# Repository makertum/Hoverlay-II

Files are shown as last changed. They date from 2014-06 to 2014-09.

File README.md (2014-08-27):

Hoverlay II
=================

<h3>Version 2.0</h3>
an modular, stackable open source vapor display.

<h2>License</h2>
All files licensed under GPL V3 http://www.gnu.org/licenses/gpl.html

<h2>BOM</h2>

<h3>Milled parts (for lasercuting: add drillholes), the material is 3mm PVC or acrylic (never put PVC into a lasercutter)</h3>
<ul>
	<li>1x becken-boden.dxf</li>
	<li>1x becken-seite-2x.dxf (contains two parts)</li>
	<li>1x becken-stirn-2x.dxf (contains two parts)</li>
	<li>1x kamin-2x.dxf (contains two parts)</li>
	<li>1x lufteinlass-2x.dxf (contains two parts)</li>
	<li>1x m-seite-logo-neu.dxf (logo is for engraving, not a cut-out)</li>
	<li>1x m-seite-schriftzug.dxf (text is for engraving, not a cut-out)</li>
	<li>2x m-stirn.dxf</li>
	<li>1x nebler-halter.dxf (contains 3 parts)</li>
</ul>

<h3>Printed parts</h3>
<ul>
	<li>12x stecker_halter.stl</li>
	<li>1x stromversorgung_1.stl</li>
	<li>1x stromversorgung_2.stl</li>
	<li>2x brightness_booster.stl (optional, for larger installations of 3+ Hoverlay II modules)</li>
	<li>4x supercomb_air.gcode (generated by supercomb_air.pde, a <a href="http://processing.org" target="_blank">processing</a> sketch)</li>
	<li>2x supercomb_fog.gcode (generated by supercomb_fog.pde, a <a href="http://processing.org" target="_blank">processing</a> sketch)</li>
</ul>

<h3>Other Materials</h3>
<ul>
	<li>4x ultrasonic atomizers</li>
	<li>1x 326mm long piece of ø25mm PVC tube (perforated with a driller) (optional/deprecated, use the brightness booster instead!)</li>
	<li>8x 80mm fans (min. 40 CFM)</li>
	<li>2x 60mm fans (for the brightness booster)</li>
	<li>2x male 3,5 mm rc car battery power connectors (for the brightness booster, i got <a href="http://www.pollin.de/shop/dt/Mzc4OTcxOTk-/Fundgrube/Modellbau/Goldkontakt_Steckerset_3_5_mm_5_Paare.html" target="_blank">these</a>)</li>
	<li>6x male 3,5 mm rc car battery power connectors (for the Hoverlay II module, i got <a href="http://www.pollin.de/shop/dt/Mzc4OTcxOTk-/Fundgrube/Modellbau/Goldkontakt_Steckerset_3_5_mm_5_Paare.html" target="_blank">these</a>)</li>
	<li>6x female 3,5 mm rc car battery power connectors (for the Hoverlay II module, i got <a href="http://www.pollin.de/shop/dt/Mzc4OTcxOTk-/Fundgrube/Modellbau/Goldkontakt_Steckerset_3_5_mm_5_Paare.html" target="_blank">these</a>)</li>
	<li>6x female 3,5 mm rc car battery power connectors (for the power supply connectors, i got <a href="http://www.pollin.de/shop/dt/Mzc4OTcxOTk-/Fundgrube/Modellbau/Goldkontakt_Steckerset_3_5_mm_5_Paare.html" target="_blank">these</a>)</li>
	<li>12x cable ring shoes (solder them to the connectors for attaching them to the stecker_halter.stl parts</li>
	<li>strong power cables, more cable shoes, solder</li>
	<li>plastics glue (for putting together the housing)</li>
	<li>double sided adhesive tape (for installing the supercombs)</li>
	<li>silicone (for water-tightening the vat, water tightening solder connections)</li>
	<li>various screws, length mostly dependend on your case-fan height</li>
	<li>appropriate power supplies for your electronics</li>
	<li>a video or still image projector. A 3000 ANSI lumen projector doesn't hurt while a overhead or dia projector will also work. LED projectors are not recommended, for holographic projections use a light-field projector and/or add a few drops of LSD to the vat*</li>
</ul>

<h2>Apps</h2>
Raw versions of all apps are now included in the repository. Mind that the code has not been cleaned up, so it might not run or export immediately, because of wrong serial port names, missing sound files, etc. Don't give up, it's easy to make them run, the code is quite straight forward.

<h2>To do</h2>
- [x] write a bom
- [x] nice power supply connector
- [ ] clean up apps code
- [ ] finish writing to do list

<h2>Credits and Licensing</h2>
Hoverlay II and all application code is licensed under <a href="http://www.gnu.org/licenses/gpl.html" target="_blank">GPL V3</a>. This project would not have
been possible without open source hard- and software. Special thanks the following open source projects, that have been used in making and/or are part of Hoverlay II:

<h3>Hardware Design:</h3>
<ul>
	<li><a href="http://www.openscad.org" target="_blank">OpenScad</a></li>
	<li><a href="http://www.processing.org" target="_blank">Processing</a></li>
</ul>
<h3>Manufacturing:</h3>
<ul>
	<li><a href="http://www.reprap.org" target="_blank">RepRap Project</a></li>
	<li><a href="http://www.repetier.com" target="_blank">Repetier</a></li>
	<li><a href="http://www.slic3r.org" target="_blank">Slic3r</a></li>
	<li><a href="http://linuxcnc.org" target="_blank">LinuxCNC</a></li>
</ul>

<h3>Application Development:</h3>
<ul>
	<li><a href="http://processing.org" target="_blank">Processing</a></li>
	<li><a href="http://kinecta.mihoo.de" target="_blank">KinectA</a> and <a href="https://github.com/OpenNI/OpenNI" target="_blank">OpenNI</a></li>
	<li><a href="https://github.com/memo/p5-MSAFluid" target="_blank">MSAFluid Processing library</a></li>
	<li><a href="http://www.sojamo.de/libraries/oscP5/" target="_blank">oscP5 Processing library</a></li>
	<li><a href="http://code.compartmental.net/tools/minim/" target="_blank">Minim Processing library</a></li>
	<li><a href="https://code.google.com/p/saitoobjloader/" target="_blank">saitoobjloader Processing library</a></li>
	<li><a href="http://arduino.cc/" target="_blank">Arduino</a></li>
</ul>

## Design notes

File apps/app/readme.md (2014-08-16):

put your exported app application files here. they will read the contents of the calibration, music and sounds subdirectories.

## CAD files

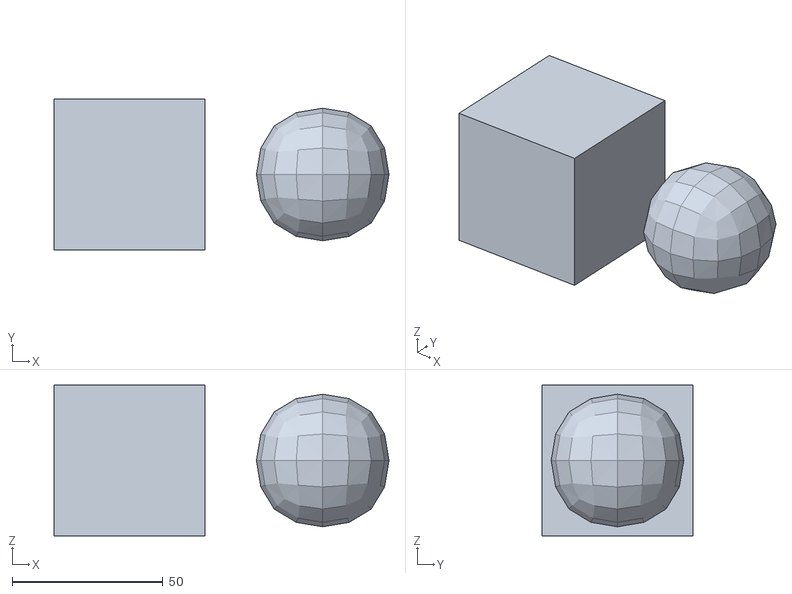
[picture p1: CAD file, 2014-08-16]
apps/sketch/Satellite/data/cube_sphere_test.obj
111.0 x 50.0 x 50.0

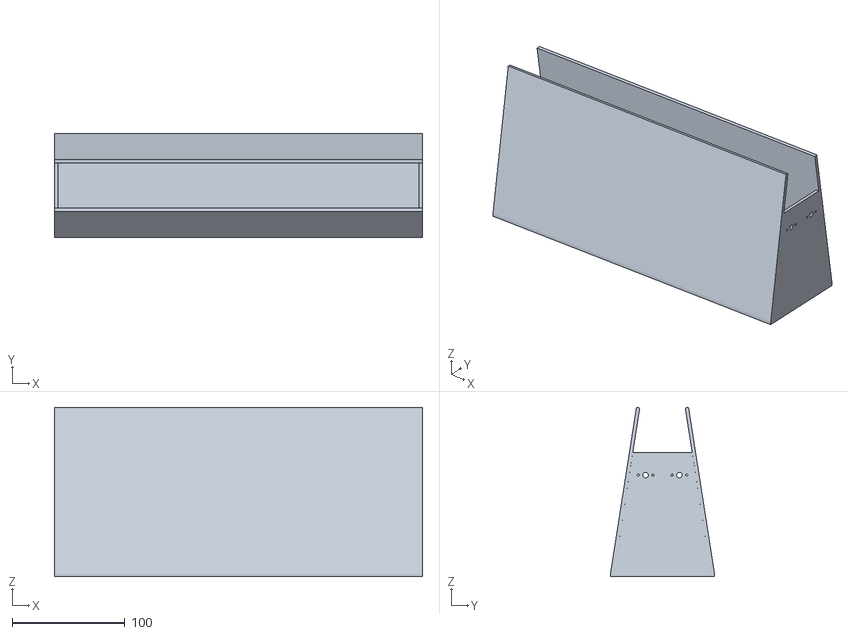
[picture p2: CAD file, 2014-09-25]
full_model/hoverlay_vat.stl
326.0 x 92.1 x 150.0

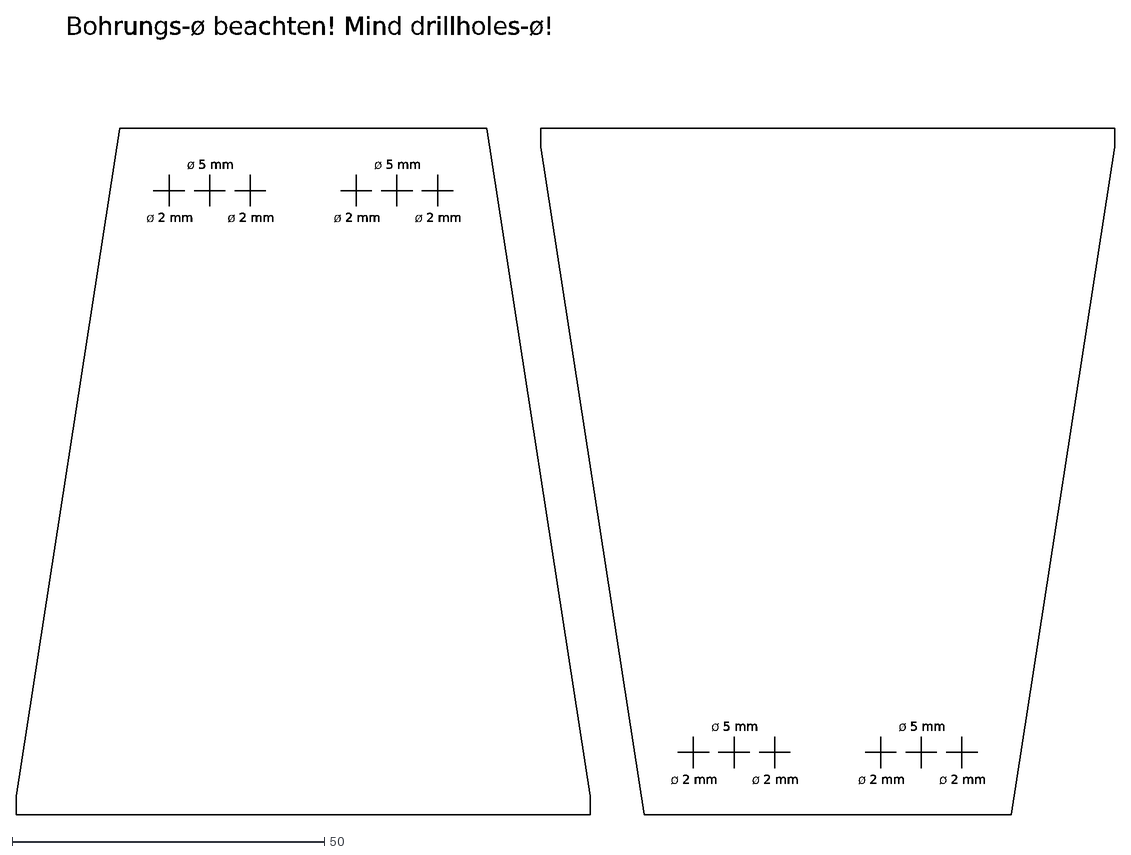
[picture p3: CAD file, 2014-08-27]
milling/dxf/becken-stirn-2x.dxf
ø 2 mm
ø 5 mm
Bohrungs-ø beachten! Mind drillholes-ø!

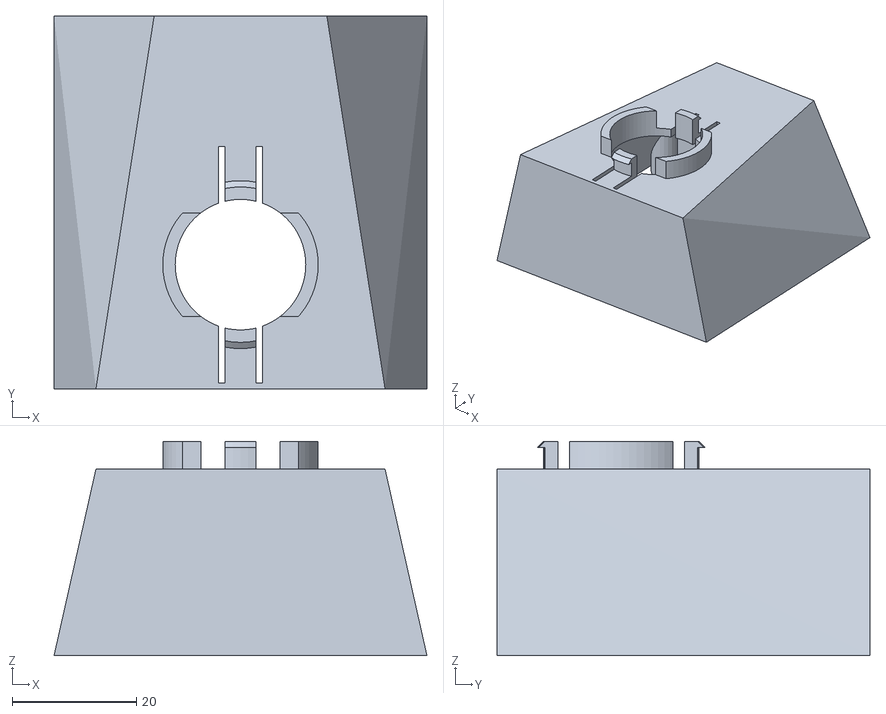
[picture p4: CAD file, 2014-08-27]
printing/brightness_booster/brightness_booster.stl
60.0 x 60.0 x 34.5

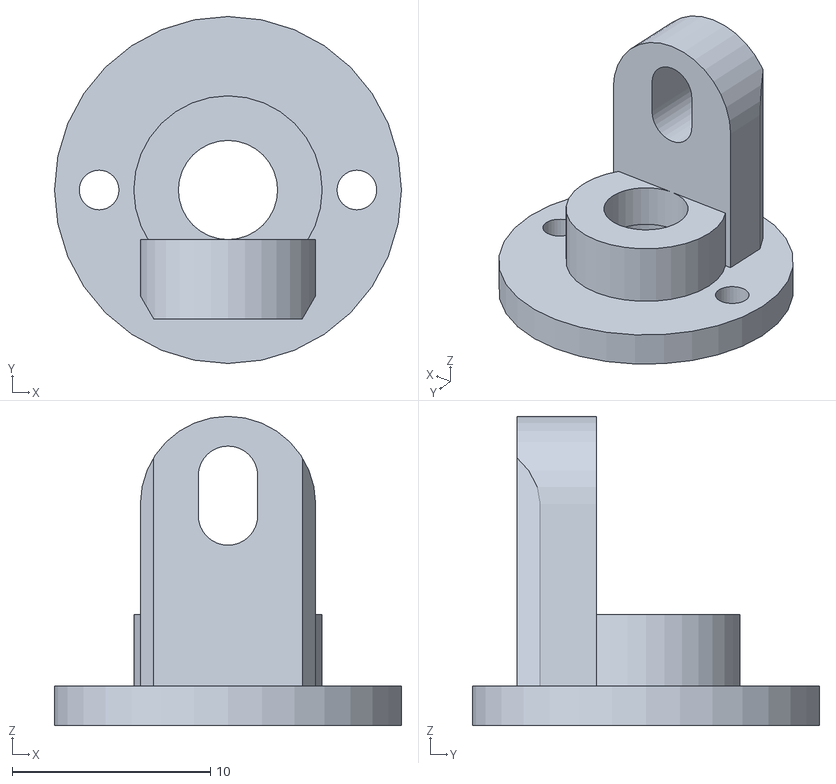
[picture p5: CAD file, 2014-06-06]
printing/stecker_halter/stecker_halter_2.stl
17.5 x 17.5 x 15.6

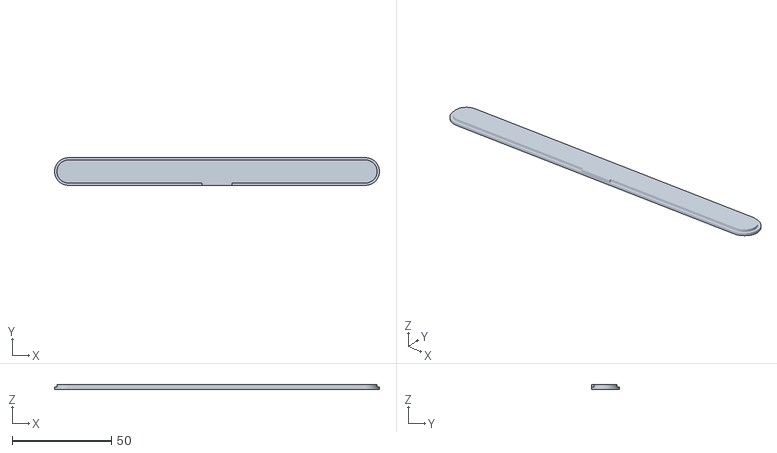
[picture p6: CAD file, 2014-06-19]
printing/stromversorgung/stromversorgung_top.stl
164.0 x 14.0 x 2.40

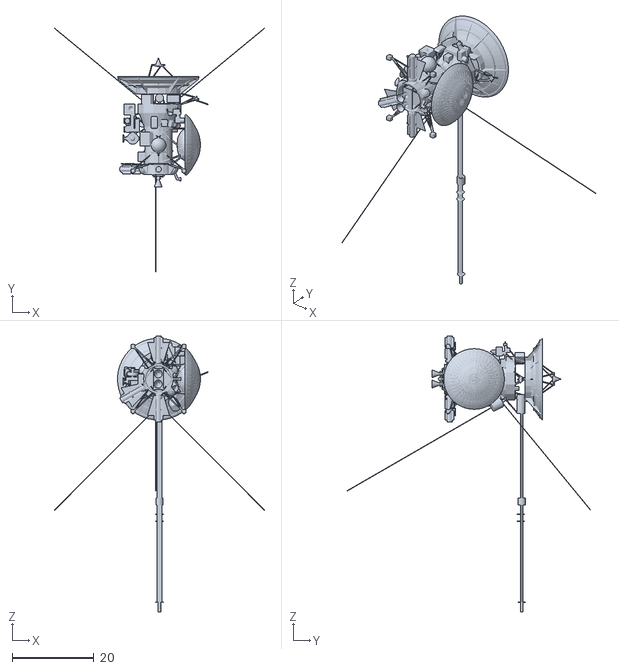
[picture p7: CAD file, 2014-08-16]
apps/sketch/Satellite/data/cassini.obj
51.4 x 59.6 x 67.5

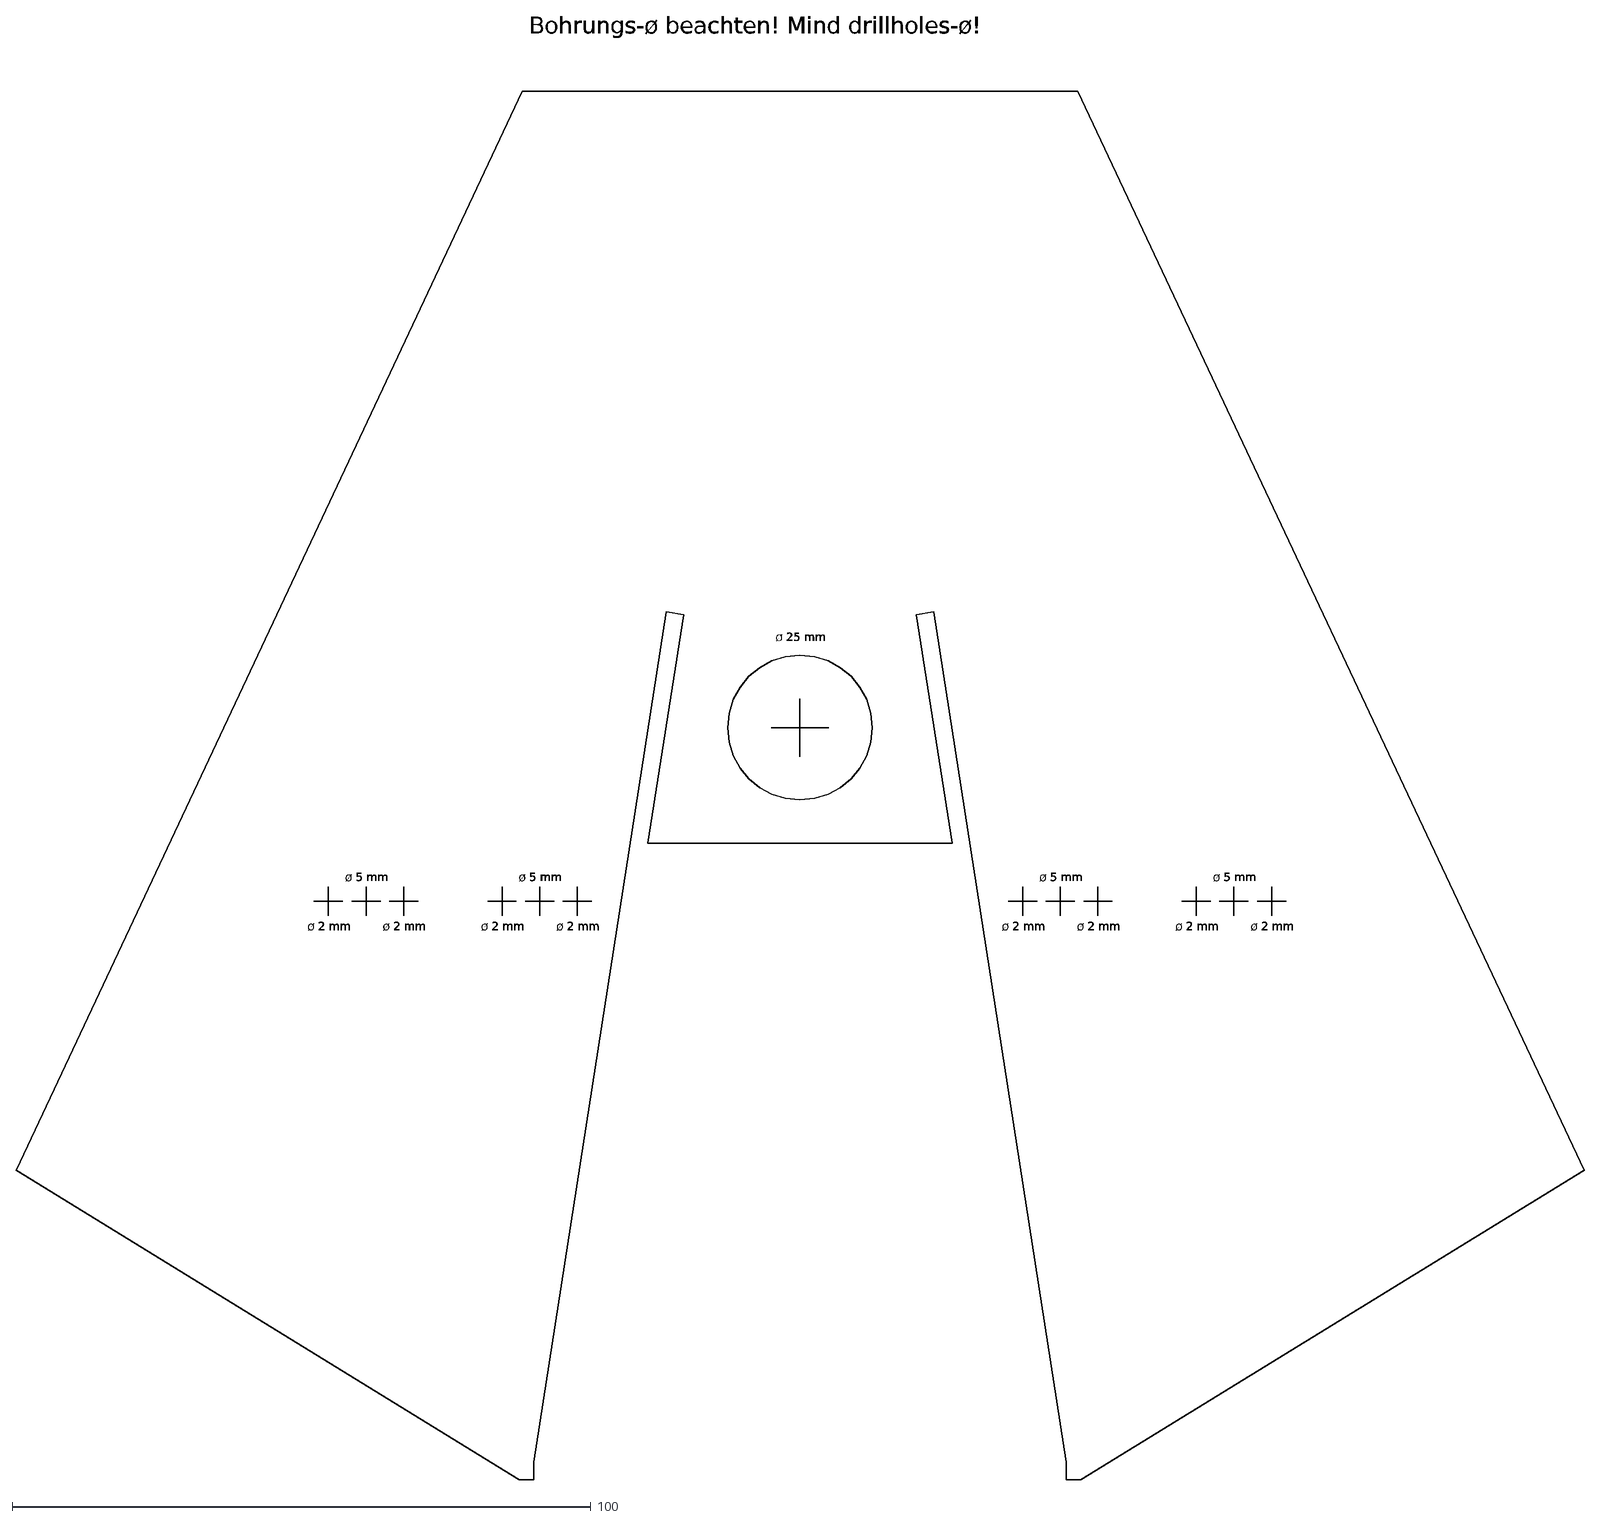
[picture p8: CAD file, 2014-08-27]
milling/dxf/m-stirn.dxf
Bohrungs-ø beachten! Mind drillholes-ø!
ø 2 mm
ø 5 mm
ø 25 mm

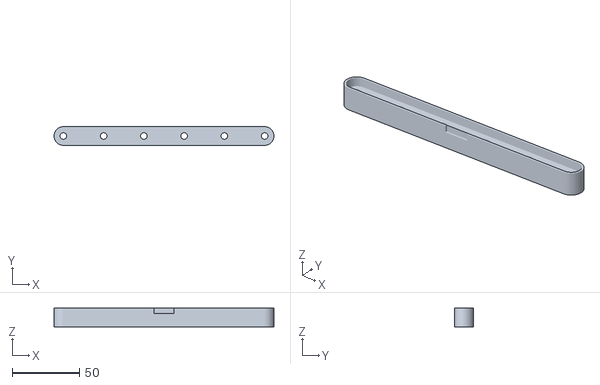
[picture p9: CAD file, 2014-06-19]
printing/stromversorgung/stromversorgung_case.stl
164.0 x 14.0 x 13.8

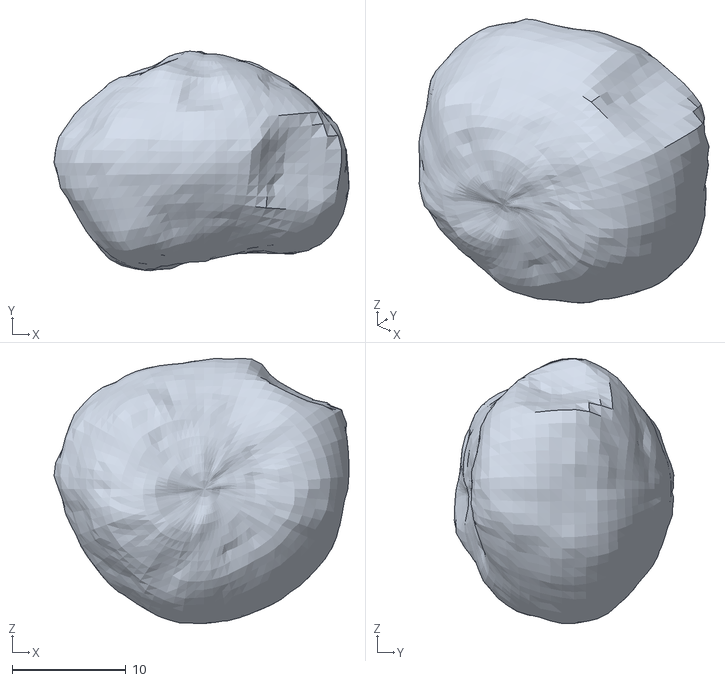
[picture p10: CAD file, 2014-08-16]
apps/sketch/Satellite/data/phobos.obj
26.0 x 19.3 x 23.4

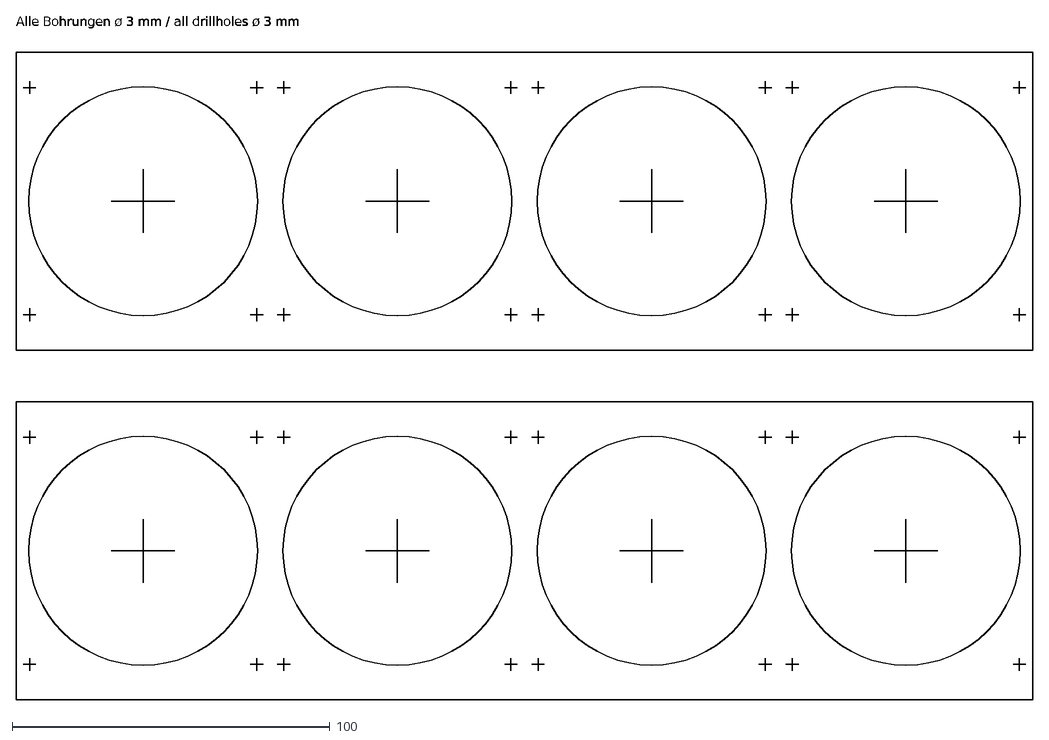
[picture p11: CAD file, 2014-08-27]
milling/dxf/lufteinlass-2x.dxf
Alle Bohrungen ø 3 mm / all drillholes ø 3 mm

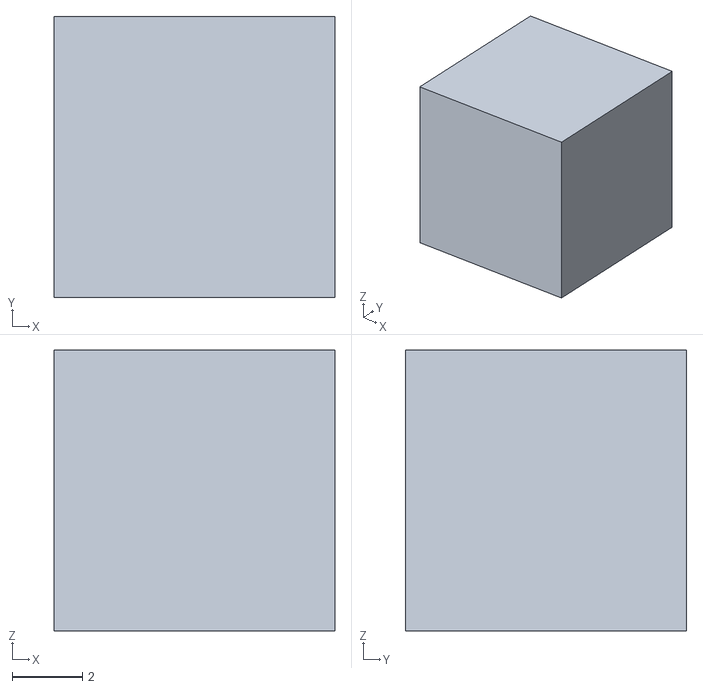
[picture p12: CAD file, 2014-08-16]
apps/sketch/Satellite/data/modo.obj
8.00 x 8.00 x 8.00

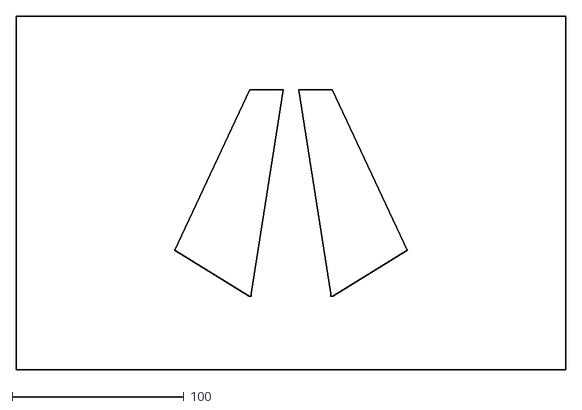
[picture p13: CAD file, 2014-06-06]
milling/dxf/m-seite-logo-neu.dxf
320.0 x 206.0

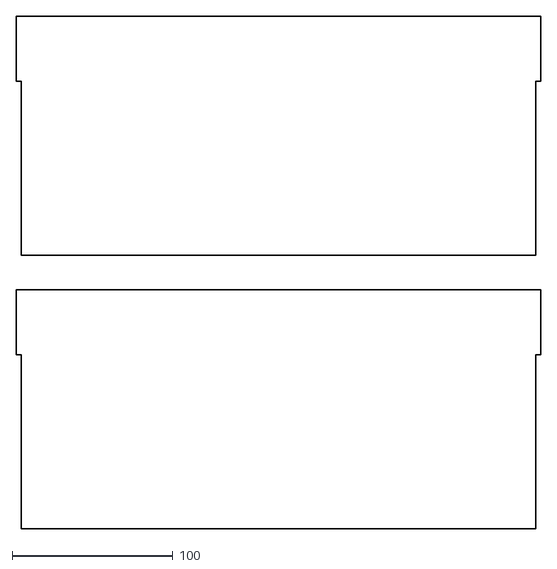
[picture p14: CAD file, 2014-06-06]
milling/dxf/becken-seite-2x.dxf
326.0 x 318.8

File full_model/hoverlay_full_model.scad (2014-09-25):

module side_plate(){
	difference(){
		translate([0,0,-3/2])
			linear_extrude(height=3){
				polygon(
					points=[
						[-48,140],		// 00
						[48,140],			// 01
						[135.5,-46.5],	// 02
						[48.5,-100],		// 03
						[46.036,-100],	// 04
						[46.036,-97],		// 05
						[23.087,50],		// 06
						[20.122,49.542],	// 07
						[26.295,10],		// 08
						[-26.295,10],		// 09
						[-20.122,49.542],// 10
						[-23.087,50],		// 11
						[-46.036,-97],	// 12
						[-46.036,-100],	// 13
						[-48.5,-100],		// 14
						[-135.5,-46.5],	// 15
						[-135.5,-46.5],	// 16
						[48,140],			// 17
					],
					paths=[
						[0,1,2,3,4,5,6,7,8,9,10,11,12,13,14,15,16,17]
					]
				);
			}
		translate([0,30,0])
			cylinder(r=25/2,h=3,center=true,$fn=32);
		translate([-75,-10,0]){
			cylinder(r=5/2,h=3,center=true,$fn=16);
				translate([-6.5,0,0])
					cylinder(r=2/2,h=3,center=true,$fn=16);
				translate([6.5,0,0])
					cylinder(r=2/2,h=3,center=true,$fn=16);
		}
		translate([-45,-10,0]){
			cylinder(r=5/2,h=3,center=true,$fn=16);
				translate([-6.5,0,0])
					cylinder(r=2/2,h=3,center=true,$fn=16);
				translate([6.5,0,0])
					cylinder(r=2/2,h=3,center=true,$fn=16);
		}
		translate([45,-10,0]){
			cylinder(r=5/2,h=3,center=true,$fn=16);
				translate([-6.5,0,0])
					cylinder(r=2/2,h=3,center=true,$fn=16);
				translate([6.5,0,0])
					cylinder(r=2/2,h=3,center=true,$fn=16);
		}
		translate([75,-10,0]){
			cylinder(r=5/2,h=3,center=true,$fn=16);
				translate([-6.5,0,0])
					cylinder(r=2/2,h=3,center=true,$fn=16);
				translate([6.5,0,0])
					cylinder(r=2/2,h=3,center=true,$fn=16);
		}
	}
}

module side_plates(){
	translate([-320/2-3/2,0,0])
		rotate([0,0,90])
			rotate([90,0,0])
				side_plate();
	translate([320/2+3/2,0,0])
		rotate([0,0,90])
			rotate([90,0,0])
				side_plate();
}


module logo_plates(){
	fpx1=65.639;
	fpy1=-95.582;
	fpx2=153.139;
	fpy2=90.918;
	angle=atan((fpy2-fpy1)/(fpx2-fpx1));
	fpoffy=-90.385;
	fpoffz=46.1;
	translate([0,fpoffy,fpoffz])
		rotate([angle,0,0])
			cube([320,206,3],center=true);
	translate([0,-fpoffy,fpoffz])
		rotate([-angle,0,0])
			cube([320,206,3],center=true);
}


module vent(){
	vx1=46.036;
	vy1=-97;
	vx2=23.087;
	vy2=50;
	angle=atan((vy2-vy1)/(vx2-vx1));
	voffy=14.626;
	voffz=75.024;
	translate([0,voffy,voffz])
		rotate([angle,0,0])
			cube([320,131.099,3],center=true);
	translate([0,-voffy,voffz])
		rotate([-angle,0,0])
			cube([320,131.099,3],center=true);
}

module air_inlets(){
	aix1=-132.38;
	aiy1=46.323;
	aix2=-42.322;
	aiy2=72.076;
	angle=atan((aiy2-aiy1)/(aix2-aix1));
	aioffy=88.4;
	aioffz=-59;
	translate([0,aioffy,aioffz])
		rotate([angle,0,0])
			air_inlet();
	translate([0,-aioffy,aioffz])
		rotate([-angle,0,0])
			air_inlet();
}

module air_inlet(){
	fan_size=80;
	fan_holes_dist=71.5;
	fan_inlet_diameter=70;
	difference(){
		cube([320,93.667,3],center=true);
		for(i=[-1.5:1.5]){
			translate([i*fan_size,0,0]){
				// FAN INLET
				cylinder(r=fan_inlet_diameter/2,h=3,center=true,$fn=32);
				// MOUNTING HOLES
				translate([-fan_holes_dist/2,-fan_holes_dist/2,0])
					cylinder(r=4/2,h=3,center=true,$fn=16);
				translate([fan_holes_dist/2,-fan_holes_dist/2,0])
					cylinder(r=4/2,h=3,center=true,$fn=16);
				translate([-fan_holes_dist/2,fan_holes_dist/2,0])
					cylinder(r=4/2,h=3,center=true,$fn=16);
				translate([fan_holes_dist/2,fan_holes_dist/2,0])
					cylinder(r=4/2,h=3,center=true,$fn=16);
			}
		}
	}
}

module housing(){
	union(){
		air_inlets();
		side_plates();
		logo_plates();
		vent();
		combs_fog();
		combs();
	}
}

module vat_side_plate(){
	difference(){
		translate([0,0,-3/2])
			linear_extrude(height=3){
				polygon(
					points=[
						[43,-97],		// 00
						[26.259,10],	// 01
						[-26.259,10],	// 02
						[-43,-97],	// 03
					],
					paths=[
						[0,1,2,3]
					]
				);
			}
		translate([-15,-10,0]){
			cylinder(r=5/2,h=3,center=true,$fn=16);
			translate([-6.5,0,0])
				cylinder(r=2/2,h=3,center=true,$fn=16);
			translate([6.5,0,0])
				cylinder(r=2/2,h=3,center=true,$fn=16);
	
		}
		translate([15,-10,0]){
			cylinder(r=5/2,h=3,center=true,$fn=16);
			translate([-6.5,0,0])
				cylinder(r=2/2,h=3,center=true,$fn=16);
			translate([6.5,0,0])
				cylinder(r=2/2,h=3,center=true,$fn=16);
		}
	}
}

module vat_side_plates(){
	translate([-320/2-3/2,0,0])
		rotate([0,0,90])
			rotate([90,0,0])
				vat_side_plate();
	translate([320/2+3/2,0,0])
		rotate([0,0,90])
			rotate([90,0,0])
				vat_side_plate();
}

module vat_hull(){
	rotate([0,90,0])
		rotate([0,0,90])
			translate([0,0,-326/2])
				linear_extrude(height=326){
					polygon(
						points=[
							[46.036,-100],	// 00
							[46.036,-97],		// 01
							[23.087,50],		// 02
							[20.122,49.542],	// 03
							[43,-97],			// 04
							[-43,-97],		// 05
							[-20.122,49.542],// 06
							[-23.087,50],		// 07
							[-46.036,-97],	// 08
							[-46.036,-100],	// 09
							[-48.5,-100],		// 10
						],
						paths=[
							[0,1,2,3,4,5,6,7,8,9,10]
						]
					);
				}
}

module vat(){
	union(){
		vat_side_plates();
		vat_hull();
	}
}

module combs(){
	vx1=46.036;
	vy1=-97;
	vx2=23.087;
	vy2=50;
	angle=90-atan((vy2-vy1)/(vx2-vx1));
	translate([-320/2,-12,100])
		rotate([angle,0,0])
			translate([0,0,-40])
				comb_air();
	translate([-320/2,12,100])
		rotate([-angle,0,0])
			translate([0,-39,-40])
				comb_air();
}

module comb_air(){
	include <elements/supercomb_air.scad>;
}

module combs_fog(){
	cfcells=60;
	cflength=320;
	cfheight=6;
	cfdepth=40;
	cfwalls=0.2;
	cfcellwidth=cflength/cfcells;
	union(){
		for(i=[-cfcells/2:cfcells/2-1]){
			translate([cfcellwidth/2+i*cfcellwidth,0,140-cfdepth/2])
				difference(){
					cube([cfcellwidth,cfheight,cfdepth],center=true);
					cube([cfcellwidth-2*cfwalls,cfheight-2*cfwalls,cfdepth],center=true);
				}
		}
	}
}
housing();
vat();

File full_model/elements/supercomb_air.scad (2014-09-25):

top_width=39;
bottom_width=39;
col_offset=0;
length=160;
height=40;
rows=12; // 16
cols=30; // 40
walls_bottom=0.3;
walls_top=0.3;
deflux=0.01;
//col_length=(length-walls)/cols;
col_length=4*(length)/(3*cols+0.5);
top_row_width=2*(top_width)/(rows+1);
bottom_row_width=2*(bottom_width)/(rows+1);

straws();
translate([length-0.125*col_length,0,0])
	straws();

module frame(){
	//real_length=col_length+(cols/2-1)*(col_length+0.5*col_length);
	real_length=length;
	box(points=[
		[
			0,
			col_offset,
			0
		],
		[
			real_length,
			col_offset,
			0
		],
		[
			real_length,
			bottom_width+col_offset,
			0
		],
		[
			0,
			bottom_width+col_offset,
			0
		],
		[
			0,
			0,
			height
		],
		[
			real_length,
			0,
			height
		],
		[
			real_length,
			top_width,
			height
		],
		[
			0,
			top_width,
			height
		]
	]);
}

module frame_cutout(){
	box(points=[
		[
			walls,
			col_offset+walls,
			0
		],
		[
			length-walls,
			col_offset+walls,
			0
		],
		[
			length-walls,
			bottom_width+col_offset-walls,
			0
		],
		[
			walls,
			bottom_width+col_offset-walls,
			0
		],
		[
			walls,
			walls,
			height
		],
		[
			length-walls,
			walls,
			height
		],
		[
			length-walls,
			top_width-walls,
			height
		],
		[
			walls,
			top_width-walls,
			height
		]
	]);
}

module straws(){
	union(){
		for(y=[0:2:rows-1]){
			for(x=[0:1:cols-1]){
				hexastraw(			
					x_bot=0.5*col_length+x*(3/4*col_length),
					y_bot=(x%2+y+1)*bottom_row_width/2+col_offset,
					z_bot=0,
					x_top=0.5*col_length+x*(3/4*col_length),
					y_top=(x%2+y+1)*top_row_width/2,
					z_top=height,
					w_bot=col_length+deflux,
					h_bot=bottom_row_width+deflux,
					w_top=col_length+deflux,
					h_top=top_row_width+deflux,
					walls_bot=walls_bottom,
					walls_top=walls_top
				);
			}
		}
	}
}

module box_ref(_length,_top_width,_bottom_width,_height,_offset){
	scaling_factor=_top_width/(_bottom_width+_offset);
	difference(){
		linear_extrude(height = _height, scale = [1,scaling_factor]){
			square ([_length,_bottom_width+_offset]);
		}
		translate([-_length,-_offset,-_height])
			linear_extrude(height = 3*_height, scale = [1,0])
				square ([3*_length,3*_offset]);
	}
}

module box(points=[[0,0,0],[100,0,0],[100,100,0],[0,100,0],[0,0,100],[100,0,100],[100,100,100],[0,100,100]]){
	polyhedron(
		points=[points[0],points[1],points[2],points[3],points[4],points[5],points[6],points[7]],
		triangles=[
			[0,5,1], // front
			[0,4,5], // front
			[3,6,7], // back
			[3,2,6], // back
			[7,5,4], // top
			[7,6,5], // top
			[1,3,0], // bottom
			[1,2,3], // bottom
			[7,0,3], // left
			[7,4,0], // left
			[5,2,1], // right
			[5,6,2]  // right
		]
	);
}

module hexagon(x_bot, y_bot, z_bot, x_top, y_top, z_top, w_bot, h_bot, w_top, h_top){
	//off_x_bot=sqrt(abs(pow(w_bot,2)-pow(h_bot,2)))/2;
	//off_x_top=sqrt(abs(pow(w_top,2)-pow(h_top,2)))/2;
	off_y_bot=h_bot/2;
	off_y_top=h_top/2;
	r_bot=w_bot/2;
	r_top=w_top/2;
	off_x_bot=0.5*r_bot;
	off_x_top=0.5*r_top;
	polyhedron(
		points=[
			// bottom
			[x_bot-r_bot,y_bot,z_bot],						// 0
			[x_bot-off_x_bot,y_bot+off_y_bot,z_bot],	// 1
			[x_bot+off_x_bot,y_bot+off_y_bot,z_bot],	// 2
			[x_bot+r_bot,y_bot,z_bot],						// 3
			[x_bot+off_x_bot,y_bot-off_y_bot,z_bot],	// 4
			[x_bot-off_x_bot,y_bot-off_y_bot,z_bot],	// 5
			// top
			[x_top-r_top,y_top,z_top],						// 6
			[x_top-off_x_top,y_top+off_y_top,z_top],	// 7
			[x_top+off_x_top,y_top+off_y_top,z_top],	// 8
			[x_top+r_top,y_top,z_top],						// 9
			[x_top+off_x_top,y_top-off_y_top,z_top],	// 10
			[x_top-off_x_top,y_top-off_y_top,z_top]		// 11
		],
		faces=[
			[0,7,6],
			[0,1,7],
			[1,8,7],
			[1,2,8],
			[2,9,8],
			[2,3,9],
			[10,9,3],
			[10,3,4],
			[11,4,5],
			[11,10,4],
			[6,5,0],
			[6,11,5],
			[11,6,7],
			[11,7,8],
			[11,8,10],
			[10,8,9],
			[5,1,0],
			[5,2,1],
			[5,4,2],
			[4,3,2]
		]
	);
}

module hexastraw(x_bot, y_bot, z_bot, x_top, y_top, z_top, w_bot, h_bot, w_top, h_top,walls_bot,walls_top){
	angle_bot=atan(h_bot/w_bot);
	angle_top=atan(h_top/w_top);
	walls_corr_bot=(h_bot-walls_bot)/h_bot;
	walls_corr_top=(h_top-walls_top)/h_top;

	difference(){
		hexagon(
			x_bot=x_bot,
			y_bot=y_bot,
			z_bot=z_bot,
			x_top=x_top,
			y_top=y_top,
			z_top=z_top,
			w_bot=w_bot,
			h_bot=h_bot,
			w_top=w_top,
			h_top=h_top
		);
		hexagon(
			x_bot=x_bot,
			y_bot=y_bot,
			z_bot=z_bot,
			x_top=x_top,
			y_top=y_top,
			z_top=z_top,
			w_bot=w_bot*walls_corr_bot,
			h_bot=h_bot-walls_bot,
			w_top=w_top*walls_corr_top,
			h_top=h_top-walls_top
		);
	}
}

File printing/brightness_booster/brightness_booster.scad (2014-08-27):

// Hoverlay II brighntness booster mk1
// created by Moritz Walter, 2014
// licensed under GPL V3
// all infos at iamnotachoice.com/hoverlay-2

// BASIC CONFIGURATION

fan_size=60; // select your fan size (in mm) here from 40, 60 or 80 (other values won't work!)

walls=1;	// thickness of printed walls
base=2;	// thickness of printed baseplate (must be a bit thicker because we're printing bridges here)
fan_dist=30;	// distance between fan and hoverlay side panel
fan_screw_diameter=2.5; // how large are your screws
fan_screw_length=8;	// how long are your screws (should be 8mm screws)
fan_screw_nipple_diameter=6; // how strong are the screw nipples ;)
fan_screw_nipple_length=fan_dist;
tube_walls=2;
tube_length=3.5;

// EXTENDED CONFIGURATION

hole_diameter=25;
snappy_diameter=27;
snappy_width=5;
snappy_clearance=1;
snappy_bendable=38;

// CONSTANTS

fan_screw_dist_80mm=71.5;
fan_screw_dist_60mm=50;
fan_screw_dist_40mm=32;

housing_p0_40mm=[-17.014,20,0];
housing_p1_40mm=[17.014,20,0];
housing_p0_60mm=[-13.892,40,0];
housing_p1_60mm=[13.892,40,0];
housing_p0_80mm=[-10.77,60,0];
housing_p1_80mm=[10.77,60,0];
housing_p2=[23.259,-20,0];
housing_p3=[-23.259,-20,0];

// PREPROCESSING

housing_p0i_40mm=[housing_p0_40mm[0]+walls,housing_p0_40mm[1]-walls,base];
housing_p1i_40mm=[housing_p1_40mm[0]-walls,housing_p1_40mm[1]-walls,base];

housing_p0i_60mm=[housing_p0_60mm[0]+walls,housing_p0_60mm[1]-walls,base];
housing_p1i_60mm=[housing_p1_60mm[0]-walls,housing_p1_60mm[1]-walls,base];

housing_p0i_80mm=[housing_p0_80mm[0]+walls,housing_p0_80mm[1]-walls,base];
housing_p1i_80mm=[housing_p1_80mm[0]-walls,housing_p1_80mm[1]-walls,base];

housing_p2i=[housing_p2[0]-walls,housing_p2[1]+walls,base];
housing_p3i=[housing_p3[0]+walls,housing_p3[1]+walls,base];

fan_center=[(housing_p2[0]+housing_p3[0])/2,(housing_p2[1]+housing_p3[1])/2+fan_size/2,fan_dist];

fan_p0=[fan_center[0]-fan_size/2,fan_center[1]+fan_size/2,fan_center[2]];
fan_p1=[fan_center[0]+fan_size/2,fan_center[1]+fan_size/2,fan_center[2]];
fan_p2=[fan_center[0]+fan_size/2,fan_center[1]-fan_size/2,fan_center[2]];
fan_p3=[fan_center[0]-fan_size/2,fan_center[1]-fan_size/2,fan_center[2]];

fan_p0i=[fan_center[0]-fan_size/2+walls,fan_center[1]+fan_size/2-walls,fan_center[2]];
fan_p1i=[fan_center[0]+fan_size/2-walls,fan_center[1]+fan_size/2-walls,fan_center[2]];
fan_p2i=[fan_center[0]+fan_size/2-walls,fan_center[1]-fan_size/2+walls,fan_center[2]];
fan_p3i=[fan_center[0]-fan_size/2+walls,fan_center[1]-fan_size/2+walls,fan_center[2]];

// TEH CODE

module tube_cutout(){
	translate([0,0,base/2])
		cylinder(r=hole_diameter/2-tube_walls,h=base,center=true, $fn=64);
}

module tube(){
	translate([0,0,-tube_length/2-walls/2])
			intersection(){
				difference(){
					cylinder(r=hole_diameter/2,h=tube_length+walls,center=true, $fn=64);
					cylinder(r=hole_diameter/2-tube_walls,h=tube_length+walls,center=true, $fn=64);
				}
			cube([hole_diameter,2/3*hole_diameter,tube_length+walls],center=true);
		}
}

module snappy(){
		intersection(){
			union(){
				translate([0,0,-tube_length-walls/2])
					difference(){
						cylinder(r1=hole_diameter/2,r2=snappy_diameter/2,h=walls,center=true, $fn=64);
						cylinder(r=hole_diameter/2-tube_walls,h=walls,center=true, $fn=64);
					}
				translate([0,0,-tube_length/2-walls/2])
					difference(){
						cylinder(r=hole_diameter/2,h=tube_length+walls,center=true, $fn=64);
						cylinder(r=hole_diameter/2-tube_walls,h=tube_length+walls,center=true, $fn=64);
					}
			}
			translate([0,0,-tube_length/2-walls/2])
			cube([snappy_width,snappy_diameter,tube_length+walls],center=true);
		}
}

module snappy_cutout(){
	translate([snappy_width/2+snappy_clearance/2,0,base/2])
		cube([snappy_clearance,snappy_bendable,base],center=true);
	translate([-snappy_width/2-snappy_clearance/2,0,base/2])
		cube([snappy_clearance,snappy_bendable,base],center=true);
	
}


module duct(){
	difference(){
		union(){
			difference(){
				if (fan_size==40){
					difference(){
						outer_duct(housing_p0_40mm, housing_p1_40mm);
						inner_duct(housing_p0i_40mm, housing_p1i_40mm);
					}
				} else if (fan_size==60){
					difference(){
						outer_duct(housing_p0_60mm, housing_p1_60mm);
						inner_duct(housing_p0i_60mm, housing_p1i_60mm);
					}
				} else if (fan_size==80){
					difference(){
						outer_duct(housing_p0_80mm, housing_p1_80mm);
						inner_duct(housing_p0i_80mm, housing_p1i_80mm);
					}
				}
				tube_cutout();
				snappy_cutout();
			}
			if (fan_size==40){
				screw_nipples(fan_screw_dist_40mm);
			} else if (fan_size==60){
				screw_nipples(fan_screw_dist_60mm);
			} else if (fan_size==80){
				screw_nipples(fan_screw_dist_80mm);
			}
		}
		if (fan_size==40){
			screw_cutouts(fan_screw_dist_40mm);
		} else if (fan_size==60){
			screw_cutouts(fan_screw_dist_60mm);
		} else if (fan_size==80){
			screw_cutouts(fan_screw_dist_80mm);
		}
	}
}

module inner_duct(housing_p0i, housing_p1i){
	polyhedron(
		points=[
			housing_p0i,
			housing_p1i,
			housing_p2i,
			housing_p3i,
			fan_p0i,
			fan_p1i,
			fan_p2i,
			fan_p3i
		],
		faces=[
			[2,1,0], 	// mount
			[3,2,0],
			[4,5,6],		// fan
			[4,6,7],
			[0,4,3],		// left
			[3,4,7],
			[2,5,1],		// right
			[6,5,2],
			[0,1,4],		// top
			[5,4,1],
			[2,3,7],		// bottom
			[2,7,6]
		]
	);
}

module outer_duct(housing_p0, housing_p1){
	polyhedron(
		points=[
			housing_p0,
			housing_p1,
			housing_p2,
			housing_p3,
			fan_p0,
			fan_p1,
			fan_p2,
			fan_p3
		],
		faces=[
			[2,1,0], 	// mount
			[3,2,0],
			[4,5,6],		// fan
			[4,6,7],
			[0,4,3],		// left
			[3,4,7],
			[2,5,1],		// right
			[6,5,2],
			[0,1,4],		// top
			[5,4,1],
			[2,3,7],		// bottom
			[2,7,6]
		]
	);
}

module screw_cutouts(fan_screw_dist){
	intersection(){
		if (fan_size==40){
			inner_duct(housing_p0i_40mm, housing_p1i_40mm);
		} else if (fan_size==60){
			inner_duct(housing_p0i_60mm, housing_p1i_60mm);
		} else if (fan_size==80){
			inner_duct(housing_p0i_80mm, housing_p1i_80mm);
		}
		union(){
			translate(fan_center){
				translate([-fan_screw_dist/2,fan_screw_dist/2,-fan_screw_length/2])
					cylinder(r=fan_screw_diameter/2, h=fan_screw_length, center=true, $fn=10);
				translate([fan_screw_dist/2,fan_screw_dist/2,-fan_screw_length/2])
					cylinder(r=fan_screw_diameter/2, h=fan_screw_length, center=true, $fn=10);
				translate([-fan_screw_dist/2,-fan_screw_dist/2,-fan_screw_length/2])
					cylinder(r=fan_screw_diameter/2, h=fan_screw_length, center=true, $fn=10);
				translate([fan_screw_dist/2,-fan_screw_dist/2,-fan_screw_length/2])
					cylinder(r=fan_screw_diameter/2, h=fan_screw_length, center=true, $fn=10);
			}
		}
	}
}
module screw_nipples(fan_screw_dist){
	intersection(){
		if (fan_size==40){
			inner_duct(housing_p0i_40mm, housing_p1i_40mm);
		} else if (fan_size==60){
			inner_duct(housing_p0i_60mm, housing_p1i_60mm);
		} else if (fan_size==80){
			inner_duct(housing_p0i_80mm, housing_p1i_80mm);
		}
		union(){
			translate(fan_center){
				translate([-fan_screw_dist/2,fan_screw_dist/2,-fan_screw_nipple_length/2])
					cylinder(r=fan_screw_nipple_diameter/2, h=fan_screw_nipple_length, center=true, $fn=20);
				translate([fan_screw_dist/2,fan_screw_dist/2,-fan_screw_nipple_length/2])
					cylinder(r=fan_screw_nipple_diameter/2, h=fan_screw_nipple_length, center=true, $fn=20);
				translate([-fan_screw_dist/2,-fan_screw_dist/2,-fan_screw_nipple_length/2])
					cylinder(r=fan_screw_nipple_diameter/2, h=fan_screw_nipple_length, center=true, $fn=20);
				translate([fan_screw_dist/2,-fan_screw_dist/2,-fan_screw_nipple_length/2])
					cylinder(r=fan_screw_nipple_diameter/2, h=fan_screw_nipple_length, center=true, $fn=20);
			}
		}
	}
}

module booster(){
	union(){
		duct();
		tube();
		snappy();
	}
}

rotate([0,180,0])
	booster();

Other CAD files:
apps/sketch/Satellite/data/phobos2.obj
apps/sketch/Satellite/data/grid_test.obj
milling/dxf/m-seite-schriftzug.dxf
milling/dxf/nebler-halter.dxf
printing/stecker_halter/stecker_halter_2.scad
milling/dxf/becken-boden.dxf
milling/dxf/kamin-2x.dxf
milling/dxf/stromversorgung-experimental.dxf
printing/stromversorgung/stromversorgung.scad

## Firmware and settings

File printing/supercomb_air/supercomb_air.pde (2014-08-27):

// Hoverlay II honeycomb gcode generator
// created by Moritz Walter, 2014
// licensed under GPL V3
// all infos at iamnotachoice.com/hoverlay-2

float top_width=39;
float bottom_width=39;// 51
float col_offset=0; //6
float total_length=160;
float total_height=40;
int rows=12; // 16
int cols=30; // 40

// calculating geometry
float col_length=4*(total_length)/(3*cols+0.5);
float top_row_width=2*(top_width)/(rows+1);
float bottom_row_width=2*(bottom_width)/(rows+1);

float nozzle_temp=255;
float bed_temp=110;

float print_speed = 40;
float travel_speed = 150;
float first_layer_speed = 0.25;
float retraction_speed = 40;
float retraction_length = 2;

float brim_distance=5;
float brim_layers=2;

float bed_width=200;
float bed_depth=180;

float material_density=0.00104; // g/mm^3

int xy_digits=3;
int z_digits=3;
int e_digits=5;

String file_name="supercomb_air.gcode";

float nozzle_diameter=0.2;
float filament_diameter=1.7;
float extrusion_width=0.3;
float layer_height=0.2;
float extrusion_multiplier=1.0;


// STATE VARS
float current_x=0;
float current_y=0;
float current_z=0;
float lastX=0;
float lastY=0;
float lastZ=0;
float current_feedrate=0;
float last_feedrate=0;
float total_extrusion=0;

float nozzle_area=nozzle_diameter*nozzle_diameter/4*PI;
float filament_area=filament_diameter*filament_diameter/4*PI;

float bed_x_offset=(bed_width-total_length)/2;
float bed_y_offset=(bed_depth-bottom_width-col_offset)/2;

String[] gcode=new String[0];

void setup() {
  startCode();
  makeThing();
  endCode();
  saveToFile();
  println("Finished. Used "+total_extrusion/1000+" m of filament");
}

void draw() {
}

void addLine(String _line) {
  gcode = (String[])append(gcode, _line);
}

void startCode() {
  addLine("G21 ; set units to millimeters");
  addLine("M190 S"+round(bed_temp)+" ; wait for bed temperature to be reached");
  addLine("M104 S"+round(nozzle_temp)+" ; set temperature");
  addLine("G28 ; home all axes");
  addLine("G1 Z5 F5000 ; lift nozzle");
  addLine("; M105; fan off");
  addLine("G92 E0 ; set extruded length zero");
  addLine("; G0 E20 ; grab some filament");
  addLine("G92 E0 ; set extruded length zero again");
  addLine("M109 S"+round(nozzle_temp)+" ; wait for temperature to be reached");
  addLine("G90 ; use absolute coordinates");
  addLine("G92 E0");
  addLine("M83 ; use relative distances for extrusion");
  addLine("M106 S127");
  addLine("G1 E"+digitize(-retraction_length, e_digits)+" F"+round(retraction_speed*60));
}

void endCode() {
  addLine("G91 ; set to relative positioning");
  addLine("G0 E-20 ; retract filament;");
  addLine("G90 ; set to absolute positioning");
  addLine("G92 E0 ; set extruded length zero");
  addLine("M104 S0 ; turn off extruder temperature");
  addLine("M140 S0 ; turn off heated bed temperature");
  addLine("G0 X195 Y175 ; move out of the way");
  addLine("M84 ; disable motors");
}


void makeThing() {
  for (float z=0.2;z<=total_height;z+=0.2) {
    println("making layer "+z);
    addLayer(z);
  }
}

void addLayer(float z) {
  travelZ(z);
  if (current_z<=layer_height*brim_layers) {
    brim(current_z);
  }
  float layer_width=map(z-layer_height/2, 0, total_height, bottom_width, top_width);
  float layer_row_width=map(z-layer_height/2, 0, total_height, bottom_row_width, top_row_width);
  float layer_col_offset=map(z-layer_height/2, 0, total_height, col_offset, 0);
  for (float y=0;y<rows;y+=2) {
    for (float x=0;x<cols;x++) {
      hexagon(
      bed_x_offset  +0.5*col_length  +x*0.75*col_length, 
      bed_y_offset  +(x%2+y+1)*layer_row_width/2+layer_col_offset, 
      z, 
      col_length, 
      layer_row_width,
      x==0, 
      y==0, 
      x==cols-1, 
      x%2==0
        );
    }
  }
}

float digitize(float _num, int _digits) {
  float factor=pow(10, _digits);
  return ((float)round(_num*factor))/factor;
}

void saveToFile() {
  saveStrings(file_name, gcode);
}

void hexagon(float x, float y, float z, float w, float h, boolean firstX, boolean firstY, boolean lastX, boolean even) {

  float x0=x-w/2;
  float x1=x-w/4;
  float x2=x+w/4;
  float x3=x+w/2;
  float x4=x+w/4;
  float x5=x-w/4;
  float x6=x-w/2;

  float y0=y;
  float y1=y+h/2;
  float y2=y+h/2;
  float y3=y;
  float y4=y-h/2;
  float y5=y-h/2;
  float y6=y;

  float e01=dist(x0, y0, x1, y1)*extrusion_width*layer_height/filament_area*extrusion_multiplier;
  float e12=dist(x1, y1, x2, y2)*extrusion_width*layer_height/filament_area*extrusion_multiplier;
  float e23=dist(x2, y2, x3, y3)*extrusion_width*layer_height/filament_area*extrusion_multiplier;
  float e34=dist(x3, y3, x4, y4)*extrusion_width*layer_height/filament_area*extrusion_multiplier;
  float e45=dist(x4, y4, x5, y5)*extrusion_width*layer_height/filament_area*extrusion_multiplier;
  float e56=dist(x5, y5, x6, y6)*extrusion_width*layer_height/filament_area*extrusion_multiplier;

  if (firstX && firstY) {
    travelXY(x0, y0);
    tract();
    extrude(x1, y1);
    extrude(x2, y2);
    extrude(x3, y3);
    extrude(x4, y4);
    extrude(x5, y5);
    extrude(x6, y6);
    travelXY(x1, y1);
  }
  else if (firstY) {
    if (even) {
      travelXY(x1, y1);
      extrude(x2, y2);
      extrude(x3, y3);
      extrude(x4, y4);
      extrude(x5, y5);
      extrude(x6, y6);
      travelXY(x1, y1);
      travelXY(x2, y2);
    }
    else {
      travelXY(x0, y0);
      extrude(x1, y1);
      extrude(x2, y2);
      extrude(x3, y3);
      extrude(x4, y4);
      extrude(x5, y5);
      travelXY(x5, y5);
      travelXY(x4, y4);
    }
  }
  else if (firstX) {
    travelXY(x5, y5);
    tract();
    extrude(x0, y0);
    extrude(x1, y1);
    extrude(x2, y2);
    extrude(x3, y3);
  }
  else if(lastX){
    travelXY(x0, y0);
    extrude(x1, y1);
    extrude(x2, y2);
    extrude(x3, y3);
    extrude(x4, y4);
  }
  else {
    if (even) {
      travelXY(x0, y0);
      extrude(x1, y1);
      extrude(x2, y2);
      extrude(x3, y3);
    }
    else {
      travelXY(x0, y0);
      extrude(x1, y1);
      extrude(x2, y2);
      extrude(x3, y3);
    }
  }
  if (lastX) {
    retract();
  }
}

void brim(float z) {
  float x_dimension=total_length;
  float y_dimension=bottom_width+col_offset;

  float x0=bed_x_offset-brim_distance;
  float x1=bed_x_offset+brim_distance+x_dimension;
  float x2=bed_x_offset+brim_distance+x_dimension;
  float x3=bed_x_offset-brim_distance;
  float x4=bed_x_offset-brim_distance;

  float y0=bed_y_offset-brim_distance;
  float y1=bed_y_offset-brim_distance;
  float y2=bed_y_offset+brim_distance+y_dimension;
  float y3=bed_y_offset+brim_distance+y_dimension;
  float y4=bed_y_offset-brim_distance;

  travelXY(x0, y0);
  tract();
  extrude(x1, y1);
  extrude(x2, y2);
  extrude(x3, y3);
  extrude(x4, y4);
  retract();
}
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

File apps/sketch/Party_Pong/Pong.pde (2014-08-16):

class Pong {
  MVector playerA, playerB, ball, ballV, ballTest, bonusBubble;
  float defaultPaddleHeight, bonusPaddleHeight, paddleHeightA, paddleHeightB, paddleWidth, paddleMargin, borderWidth, borderDepth, bonusBubbleRadius, ballRadius, fieldWidth, fieldHeight, startV, vInc, rAnge;
  int bonusBubbleCounter, bonusBubbleDuration, bonusCounterA, bonusCounterB, bonusDuration;
  boolean contactPA, contactPB, contactT, contactB, paused;
  char lastContact;
  Pong(float _width, float _height) {
    paddleMargin=100;
    paddleWidth=30;
    defaultPaddleHeight=150;
    bonusPaddleHeight=300;
    ballRadius=15;
    paddleHeightA=defaultPaddleHeight;
    paddleHeightB=defaultPaddleHeight;
    borderWidth=5;
    borderDepth=5;
    fieldWidth=_width;
    fieldHeight=_height;
    startV=5;
    vInc=0.1;
    rAnge=radians(45);
    playerA=new MVector(-fieldWidth/2+paddleMargin, 0, 0);
    playerB=new MVector(fieldWidth/2-paddleMargin, 0, 0);
    ball=new MVector(0, 0, 0);
    if (random(1)>0.5) {
      ballV=new MVector(startV, 0, 0);
    } else {
      ballV=new MVector(-startV, 0, 0);
    }
    ballV.zRotateVector(random(0, rAnge)-rAnge/2);
    contactPA=false;
    contactPB=false;
    contactT=false;
    contactB=false;
    paused=true;
    lastContact=' ';

    bonusBubbleRadius=50;
    bonusBubble=new MVector(0, 0, 0);
    bonusBubbleCounter=0;
    bonusCounterA=0;
    bonusCounterB=0;
    bonusBubbleDuration=round(30*frameRate);
    bonusDuration=round(30*frameRate);
  }

  void frame() {
    if (!paused) {
      //getInputs();
      bonus();
      collisions();
    }
    drawElements();
  }

  void pause() {
    paused=true;
  }
  void run() {
    paused=false;
  }

  void setPlayerA(float _y) {
    float yA=constrain(_y, -fieldHeight/2+paddleHeightA/2, fieldHeight/2-paddleHeightA/2);
    playerA.set(playerA.x, yA, playerA.z);
  }

  void setPlayerB(float _y) {
    float yB=constrain(_y, -fieldHeight/2+paddleHeightB/2, fieldHeight/2-paddleHeightB/2);
    playerB.set(playerB.x, yB, playerB.z);
  }
  /*
  void getInputs() {
   float yA=constrain(mouseY-height/2, -fieldHeight/2+paddleHeightA/2, fieldHeight/2-paddleHeightA/2);
   float yB=constrain(mouseY-height/2, -fieldHeight/2+paddleHeightB/2, fieldHeight/2-paddleHeightB/2);
   playerA.set(playerA.x, yA, playerA.z);
   playerB.set(playerB.x, yB, playerB.z);
   }
   */

  void drawElements() {
    noStroke();
    ellipseMode(RADIUS);
    if (bonusBubbleCounter>0) {
      //stroke(0);
      //strokeWeight(1);
      fill(0, 255, 0);
      pushMatrix();
      translate(bonusBubble.x, bonusBubble.y, bonusBubble.z);
      sphere(bonusBubbleRadius);
      popMatrix();
    }
    noStroke();
    //stroke(0);
    //strokeWeight(0.5);
    fill(255);
    pushMatrix();
    translate(ball.x, ball.y, ball.z);
    sphere(ballRadius);
    popMatrix();
    
    // borders
    noFill();
    stroke(255);
    pushMatrix();
      translate(0,fieldHeight/2+ballRadius,-borderDepth/2);
      box(fieldWidth,borderWidth,borderDepth);
    popMatrix();
    pushMatrix();
      translate(0,-fieldHeight/2-ballRadius,-borderDepth/2);
      box(fieldWidth,borderWidth,borderDepth);
    popMatrix();
    pushMatrix();
      translate(-fieldWidth/2-ballRadius,0,-borderDepth/2);
      box(borderWidth,fieldHeight,borderDepth);
    popMatrix();
    pushMatrix();
      translate(fieldWidth/2+ballRadius,0,-borderDepth/2);
      box(borderWidth,fieldHeight,borderDepth);
    popMatrix();
    
    
    
    stroke(0);
    strokeWeight(1);
    fill(255);
    // playerA paddle
    pushMatrix();
      translate(playerA.x-paddleWidth, playerA.y, playerA.z);
      box(paddleWidth, paddleHeightA, paddleWidth);
    popMatrix();
    // playerB paddle
    pushMatrix();
      translate(playerB.x+paddleWidth, playerB.y, playerB.z);
      box(paddleWidth, paddleHeightB, paddleWidth);
    popMatrix();
  }

  void bonus() {
    bonusBubbleDuration=round(30*frameRate);
    bonusDuration=round(30*frameRate);
    if (bonusBubbleCounter==0) {
      if (random(10*frameRate)<1.0) {
        sp.play("smw_vine.wav");
        bonusBubble=new MVector(random(fieldWidth/2)-fieldWidth/4, random(fieldHeight/2)-fieldHeight/4, 0);
        bonusBubbleCounter=bonusBubbleDuration;
        println("creating bonus bubble!");
      }
    } else {
      bonusBubbleCounter--;
      if (bonusBubbleCounter==0) {
        sp.play("smw_stomp_bones.wav");
      }
    }

    if (bonusCounterA>0) {
      paddleHeightA = bonusPaddleHeight;
      bonusCounterA--;
    } else {
      paddleHeightA = defaultPaddleHeight;
    }
    if (bonusCounterB>0) {
      paddleHeightB = bonusPaddleHeight;
      bonusCounterB--;
    } else {
      paddleHeightB = defaultPaddleHeight;
    }
  }
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

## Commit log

2014-06-06 initial commit
    all the files are already there
    [becken-boden.dxf, becken-seite-2x.dxf, becken-stirn-2x.dxf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]
2014-06-15 cleanup
    fixed stecker_halter2.stl, deleted stecker_haltser_2.gcode
    [stecker_halter_2.scad]
2014-06-19 added power connector
    two stl files for the power connector can now be found in the directory
    „printing“
    [stromversorgung.scad, stromversorgung_1.stl, stromversorgung_2.stl]
2014-06-19 added bom
    added bom
2014-08-16 added sketches for apps
    [cassini.obj, cube_sphere_test.obj, grid_test.obj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]
2014-08-27 added brightness booster
    added a 3d-printable opensscad model (including rendered stl) for the
    brightness booster
    [brightness_booster.scad, brightness_booster.stl]
2014-08-27 added info texts to milling files
    milling files now contain information about drill-holes diameters etc.
    [becken-stirn-2x.dxf, lufteinlass-2x.dxf, m-stirn.dxf]
2014-08-27 minor changes
    [brightness_booster.scad, stecker_halter_2.scad, stromversorgung.scad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]
2014-09-25 added full cad model
    [hoverlay_full_model.scad, hoverlay_vat.stl, supercomb_air.scad]
